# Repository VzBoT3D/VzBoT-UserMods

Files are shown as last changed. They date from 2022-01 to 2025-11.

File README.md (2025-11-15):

# VzBoT UserMods repository

Welcome to the VzBoT UserMods repository, here you may find community mods for the VzBoT 3D-printer.

<a href="https://discord.gg/Jj5C7q4j" target="_blank">Discord Shield</a>

*Remember to update this README when uploading new mod!*

There is a [contributing guide available here](./CONTRIBUTING.md).

## Directory structure

Create a folder containing your name (without spaces) and create a folder for your mod(s).

Suggested directory layout for your mod:
- creator_name/
  - mod_name/
    - README.md with a description, optionally build instructions and required parts
    - stl/ folder with stereolithographical models, oriented correctly for printing
    - cad/ folder with original design files (STEP, F3D, Scad, etc.) (optional)
    - doc/ folder with supported documentation (optional)
    - images/ folder with screen shots/renders/etc.

## Table structure

Update the following table with the information about your mod:
- Your name
- A link to your sub-folder
- A short description of your mod
- The build difficulty:
  - :green_heart: for :green_heart: (Easy)
  - :blue_heart: for :blue_heart: (Intermediate)
  - :heart: for :heart: (Advanced)

like so:
`
| Creator | [Mod title](link) | ✔️/✖️ | ✔️/✖️ | Description | Difficulty `

---

## Mods

| Creator | Mod title | Description | [Vz330](https://github.com/VzBoT3D/VzBoT-Vz330) | [Vz235](https://github.com/VzBoT3D/VzBoT-Vz235) | Difficulty
| --- | --- | --- | --- | --- | --- |
| example | [Example mod](./creator_here/mod_folder_name)| Example entry for the table | ✔️ | ✔️ | :green_heart::blue_heart::heart: |
| airox | [VZ235 Tophat](./airox/vz235_tophat)| A tophat for the vz235 | ✖️ | ✔️ | :green_heart: |
| AdderMk2 | [Patch_Cura](./AdderMk2/Patch_Cura) | Updates 2020 Tronxy profiles in Cura | ✔️ | ✔️ | :blue_heart: |
| CapnKrunchy | [Aluminum Z WAGO Mount](./CapnKrunchy/Aluminum_Z_WAGO_Mount) | WAGO mount for Aluminum Z bed assembly | ✔️ | ✖️ | :green_heart: |
| catalinutzz| [Hemera mount](./catalinutzz/hemera-mount) | Hemera mount for the VZ Printhead | ✔️ | ✔️ | :green_heart: |
| ckvsoft | [CPAP_back_panel_tube_mount_VZ330](./ckvsoft/CPAP_back_panel_tube_mount_VZ330)| CPAP back panel tube mount VZ330. | ✔️ | ✖️ | :green_heart: |
| ckvsoft | [WaveShare](./ckvsoft/waveshare_5inch_DSI_LCD)| WaveShare 5inch DSI LCD. | ✔️ | ✔️ | :green_heart: |
| der-pw | [HBVCam-3M2111_corner-mount](./der-pw/HBVCam-3M2111_corner-mount)| HBVCam-3M2111 corner-mount | ✖️ | ✔️ | :green_heart: |
| edsped | [Bowden Collet Adapter](./edsped/) | Bowden Collet Adapter  | ✔️ |  ✔️ | :green_heart: |
| EduardoMDSousa  | [Vz-Printhead Printed MGN12H](./EduardoMDSousa/Vz-Printhead-Printed-MGN12H) | VzPrinthead Printed MGN12H | ✔️ | ✔️ | :green_heart: |
| | [Vz-Printhead-Printed_Standoffs-MGN12](./EduardoMDSousa/Vz-Printhead-Printed_Standoffs-MGN12) | Vz-Printhead-Printed_Standoffs-MGN12 | ✔️ | ✔️ | :green_heart: |
| | [Vz-Printhead-Printed-MGN12H-Orbiter-1.5-Mood](./EduardoMDSousa/Vz-Printhead-Printed-MGN12H-Orbiter-1.5-Mood) | Vz-Printhead-Printed-MGN12H-Orbiter-1.5-Mood | ✔️ | ✔️ | :green_heart: |
| | [Vz-Printhead Printed Standoffs MGN12](./EduardoMDSousa/Vz-Printhead-Printed_Standoffs-MGN12) | Vz-Printhead Printed Standoffs MGN12 | ✔️ | ✔️ | :green_heart: |
|Glizzynator | [M4_Spool_Holder](./Glizzynator/M4_Spool_Holder)| Modifies the spool holder to use M4 screws instead of M3 | ✔️ | ✔️ | :green_heart: |
| jpbnto | [Y endstop](./jpbnto/yendstop) | Y-endstop using the Tronxy XS5A switch | ✔️ | ✖️ | :green_heart: |
| | [VzHextrudort heavy back plate](./jpbnto/vzhextrudort_heavy_back_plate) | Y-endstop using the Tronxy XS5A switch | ✔️ | ✖️ | :green_heart: |
| jurisv | [SLA CPAP Trihorn](./jurisv/sla_cpap_trihorn) | CPAP Trihorn Fan ducts for SLA printers as single piece | ✔️ | ✖️ | :green_heart: |
| karnadi | [NF Crazy front face](./karnadi/NF_Crazy_2510_BLTouch) | NF Crazy front face 2510 fan with BLTouch mount | ✔️ | ✔️ | :green_heart: |
| | [VzHextrudort pneumatic coupler](./karnadi/VzHextrudort_pneumatic_coupler) | VzHextrudort pneumatic PTFE coupler | ✔️ | ✔️ | :green_heart: |
| keefo | [vent hose adapter](./keefo/vent_hose_adapter) | vent hose adapter | ✔️ | ✖️ | :green_heart: |
| knarfie | [12mm Linear Rod](./knarfie/12mm_rods) | Mod for 12mm linear rods | ✔️ | ✖️ | :green_heart: |
| | [Idler Shoulder](./knarfie/shoulder_idler) | Idler mounts with spots for shoulder bolts  | ✔️ | ✖️ | :green_heart: |
| | [Trihorn](./knarfie/trihorn_duct) | Trihorn duct for the VZ Printhead | ✔️ | ✔️ | :green_heart: |
| MadduxVape | [Vz330 Duet Config](./MadduxVape) | Vz330 AWD Config for Duett board| ✔️ |  ✖️ | :green_heart: |
| marbocub | [Vz330 Y-Gantry-1515](./marbocub/Vz330_Y-Gantry-1515) | Vz330 Y-Gantry for 1515 size gantry | ✔️ |  ✖️ | :green_heart: |
| mdwasp | [Swappable Exhaust Tube](./mdwasp/swappable_exhaust_tube) | Hot-swappable exhaust tube | ? | ✔️ | :green_heart: |
| panik988 | [Sherpa + NF Crazy front face (bracket)](./panik988/sherpa_nf_crazy_bracket) | NF Crazy Face Mount with bracket for Sherpa | ✔️ | ✔️ | :green_heart: |
| pbsuper | [VZTrident](./pbsuper/VZTrident)| Tripple Z for VZbot complete printer. | ✔️ | ✔️ | :blue_heart: |
| | [Quickdraw](./pbsuper/Quickdraw)| Quickdraw for Alu Printhead. | ✔️ | ✔️ | :green_heart: |
| | [Brace_Dancer](./pbsuper/Brace_Dancer)| Brace for Dancer so Fanduct can't move sideways. | ✔️ | ✔️ | :green_heart: |
| Polar_Ted  | [VZ HextrudORT mount](./Polar_Ted/VZ_HextrudORT_High_Motor_Mount_for_EVA/) | VZ HextrudORT high motor mount for EVA print head and V6 hot end | ✔️ |  ✔️ | :green_heart: |
| | [VZ Sexbolt Z Endstop](./Polar_Ted/Sexbolt_Sidepiece_Z_Switch/) | Sexbolt side mounted Z endstop for VZ bed frame  | ✔️ |  ✔️ | :green_heart: |
| | [VZ 330 Skirt Set](./Polar_Ted/VZ330_skirt/ ) | VZ 3330 SKirt Set with V0 Display | ✔️ | ✖️ | :green_heart: |
| | [X_Y_Pully_Height_Gauge](./Polar_Ted/X_Y_Pully_Height_Gauge/) | X Y pully height gauge  | ✔️ |  ✔️ | :green_heart: |
| | [X_Y Motor Support](./Polar_Ted/X_Y_Motor_support/) | Support shelf for X and Y motors  | ✔️ |  ✔️ | :green_heart: |
| Rac | [MGN9 Gantry](./Rac/MGN9_gantry) | MGN9 gantry | ✔️ | ✔️ | ✖️ | :blue_heart: |
| rilmar | [X5SA Z](./rilmar/X5SA_Z) | X5SA Z | ✔️ | ✔️ | :green_heart: |
| RODAM 3D | [180_Hinges](./RODAM_3D/180_Hinges/) | 180 Hinges for full door open  | ✖️ |  ✔️ | :green_heart: |
| | [2WD_2_COLOR_SCREW_PACK](./RODAM_3D/2WD_2_COLOR_SCREW_PACK/) | 2 color Idler with mod for screw kit  | ✖️ |  ✔️ | :green_heart: |
| SFINAE | [Rapido HF mount](./SFINAE/Rapido_HF_30mm_fan) | Rapido HF mount for 30mm fan | ✔️ | ✔️ | :green_heart: |
| Skysi | [Beefy X-Endstop](./Skysi/Beefy%20X-Endstop) | Beefed up Enstop for X | ✔️ | ✔️ | :green_heart: |
| SSerpente  | [Klicky probe](./SSerpente/Klicky%20probe%20Vzbot) | Klicky probe mount | ✔️ | ✔️ | :green_heart: |
| treintjes  | [Skirt](./treintjes/VzBot_Skirt) | Skirt for the VZ-Bot to house electronics under the frame | ✔️ |  ✖️ | :green_heart: |
| MadduxVape | [Vz330_Duet_Config](./MadduxVape) | Vz330 AWD Config for Duett board| ✔️ |  ✖️ | :green_heart: |
| zxzimeng  | [12mm rod aligner](./zxzimeng/12mm_aligner/) | 12mm Z Rod Aligner  | ✖️ |  ✔️ | :green_heart: |
| Lobod | [VzHextrudORT Optical Filament Sensor](./Lobod/VzHextrudORT_Filament-Sensor/) | Optical Filament sensor for printed VzHextrudORT | ✔️ | ✔️ | :heart: |

<sub>Credits to [VoronDesign/VoronUsers](https://github.com/VoronDesign/VoronUsers)</sub>

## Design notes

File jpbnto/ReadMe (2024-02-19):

YendStop.stl - using the stock tronxy x5sa limit switch, mounting position front left or rear right
Added vz hextrudort heavy backplate (note: gear spacing is for BMG clone gears)
Added klicky-00 fan duct.stl

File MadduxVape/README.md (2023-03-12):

Vz330 built from a folgertech ft5 frame 
duet wifi with a duex board this firmware is designed with cpap fan setup can easily be modified to your needs.
go through basic setup recieve updates replace files with the once included in zip folder and make the minor changes for your machine
has bl touch installed

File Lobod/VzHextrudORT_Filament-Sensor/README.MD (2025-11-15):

# Better filament sensor for VzHextrudORT

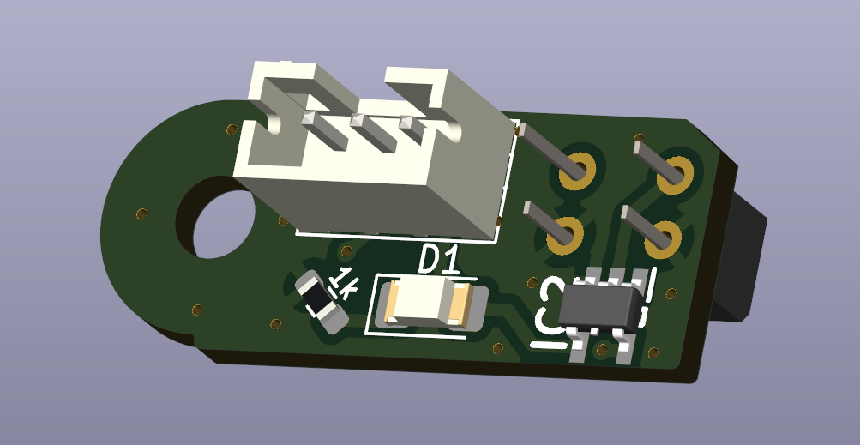
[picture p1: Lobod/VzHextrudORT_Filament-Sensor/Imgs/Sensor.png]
Sensor


Based on ERCF Binky and has the same BOM.
Uses similar principle as hall effect filament sensor, but utilizes optical path blocking for triggering.

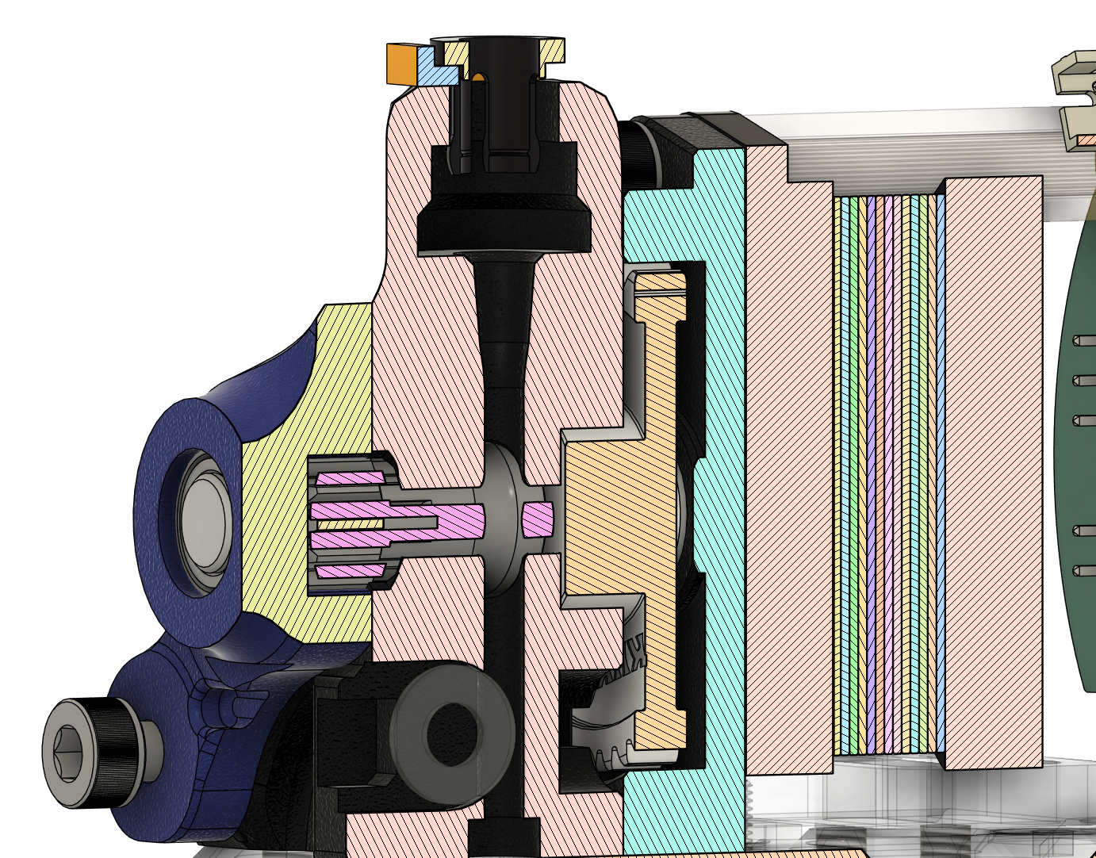
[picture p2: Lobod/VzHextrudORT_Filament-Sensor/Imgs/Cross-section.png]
Cross-section

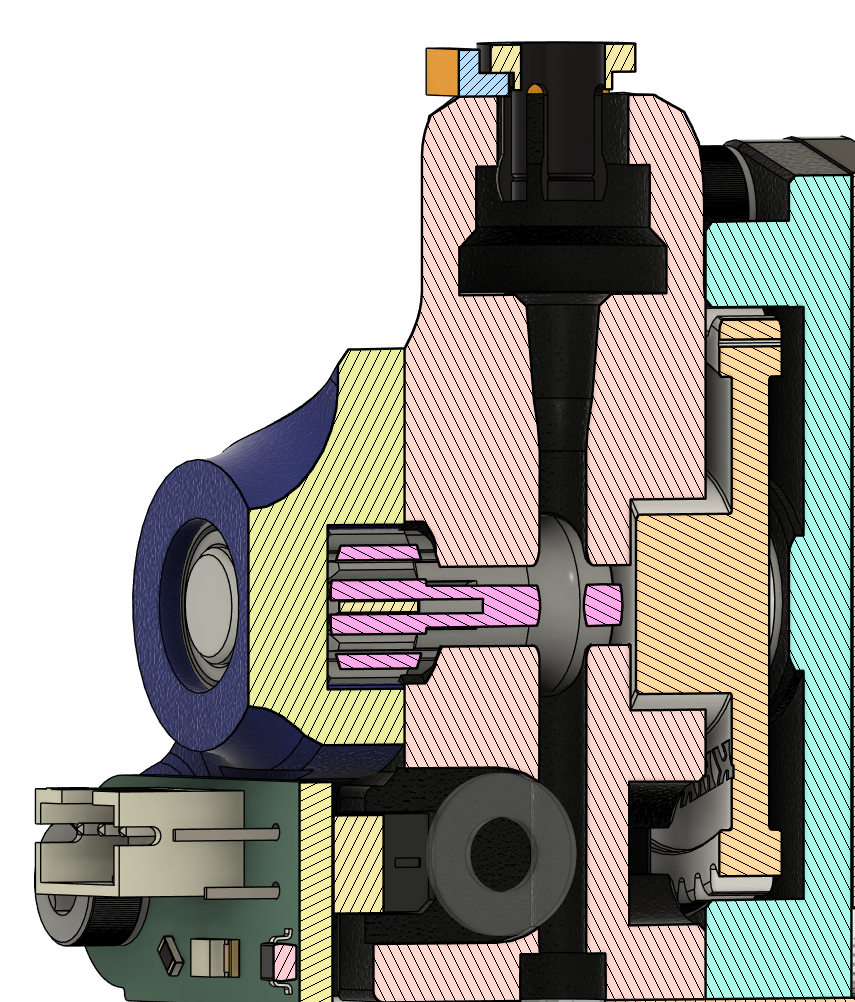
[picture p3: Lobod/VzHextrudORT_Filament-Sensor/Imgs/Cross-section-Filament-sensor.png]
Cross-section


# BOM
The same as in the original Extruder **except 6x3mm magnet**

# PCB BOM
| Component | Symbol  | Footprint |
|---|:---|:---|
Capacitor 0.1µF|C2|0603
Resistor 10K|R1|0603
Resistor 1K|R2|0603
Resistor 330R|R3|0603
LED Diode|D1|1206
EE-SX1103|IC1|EESX1103
SN74LVC1G14DBVR|IC1|SOT95P280X145-5N
JST PH 3pin|J1|JST_PH_B3B-PH-K_1x03_P2.00mm_Vertical

Interactive BOM can be found in ./PCB/BOM/ibom.html

# Build
1. Order PCB from a manufacturer.
    Ones I have tested in the past: OSHPark, JLCPCB, PcbWay.

2. Solder all parts to their coresponding places (for now there is no possibility to get soldered sensors).

3. Print included STLs (You may use supports in magnet section).

4. Place 6x3mm Magnet in the printed slot.

5. Press fit sensor into the printed base.

6. Enjoy!

# PCB Images
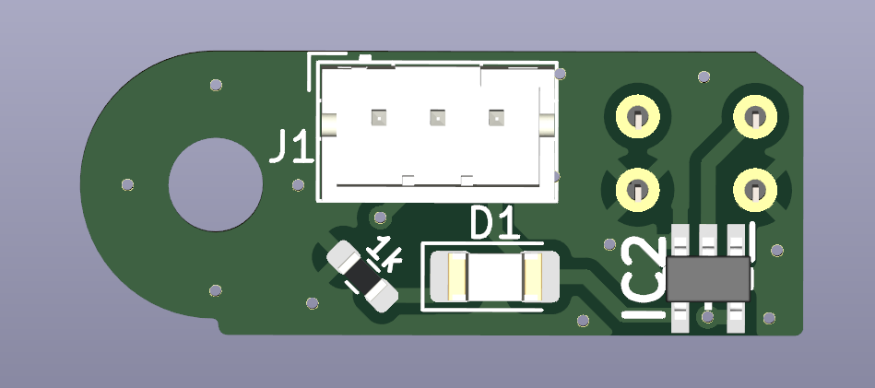
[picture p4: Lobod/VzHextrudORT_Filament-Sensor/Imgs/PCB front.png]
PCB-Front

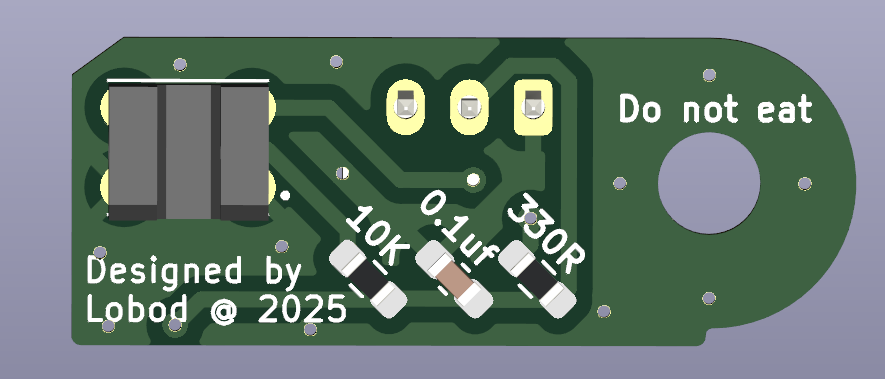
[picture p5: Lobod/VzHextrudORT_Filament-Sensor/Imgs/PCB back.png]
PCB-Back


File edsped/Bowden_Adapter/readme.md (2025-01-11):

Bowden Clip Adapter Using Spec'ed Mellow Collets, LARGE, and E3D Collets, SMALL.

I can't remember what length of screw was originally provided with the extruder but will need at least a 20mm long screw.

Print with top of adapter face down on print surface as oriented in the stl file, supports not needed.

Files on printables...

https://www.printables.com/model/486241-bowden-clip-adapter-for-vz-hextrudort-cnc-using-th

https://www.printables.com/model/420994-bowden-clip-adapter-for-vz-hextrudort-cnc-using-th

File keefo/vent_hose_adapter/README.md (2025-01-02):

this adapter can install on the outside of the vzbot exhaust filter, to connect a 3inch vent hose.

BOM:

1. M3x30mm screws x 4. (vzbot offical doc use 25mm M3 here)
2. A 3 inch flexible vent hose, length based on your needs. Like this one on amazon: https://a.co/d/2pFttcT

Print with:
* 0.2mm layer height. 
* with support, 
* 15%~30% infill.
* Nice to print it in ABS, PLA also works.

If you use this hose, you can remove the hepa filter to increase the air flow. You can save some money on buying hepa filter.  

I kept the activated carbon vent filter in to prevent bugs coming.

Showcase:

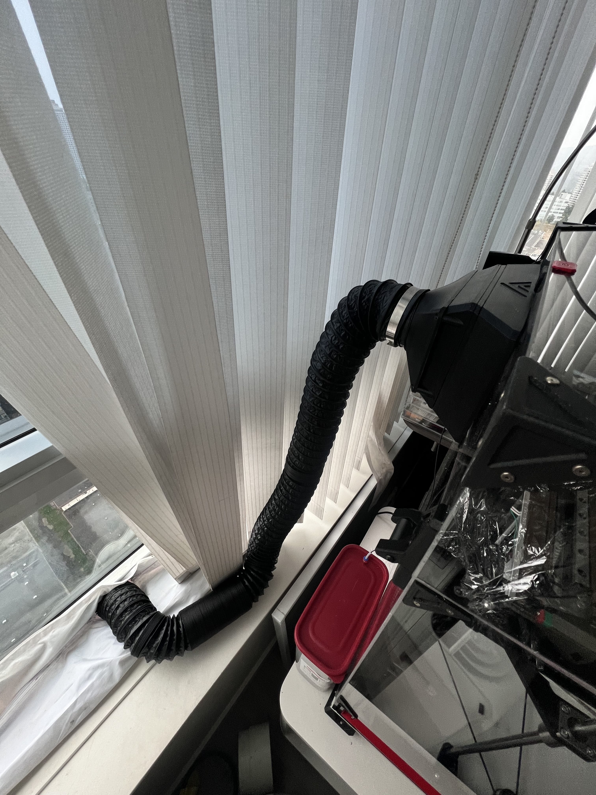
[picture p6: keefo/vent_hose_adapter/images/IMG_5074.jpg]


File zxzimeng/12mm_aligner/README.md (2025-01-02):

12mm Rod Aligner for [knarfie's 12mm rod mod](https://github.com/VzBoT3D/VzBoT-UserMods/tree/master/knarfie/12mm_rods)  
Drop in for the [10mm Aligner](https://github.com/VzBoT3D/VzBoT-Vz235/blob/main/Assemblies%20%26%20STL/Tools/Z%20allignment%20tool%2010mm%20rod%20VZ235%20VZ%20printhead.stl), using the same center position.

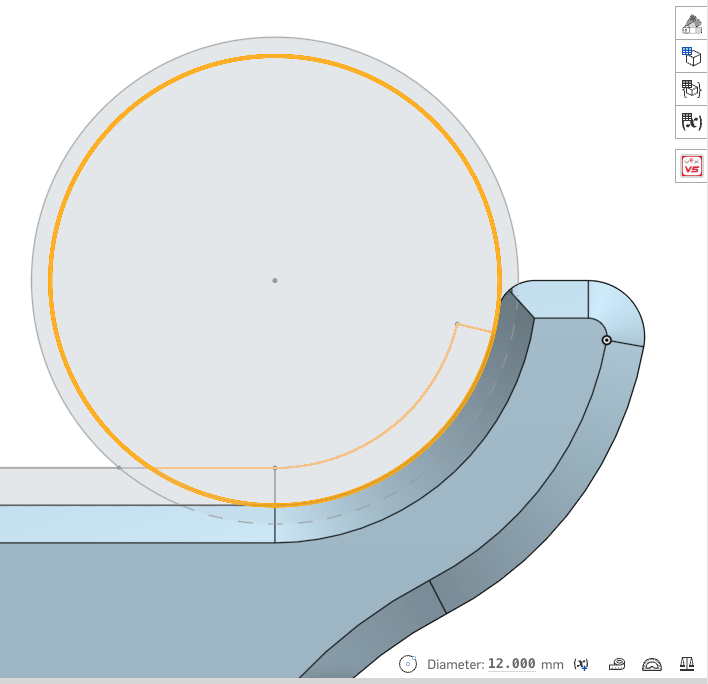
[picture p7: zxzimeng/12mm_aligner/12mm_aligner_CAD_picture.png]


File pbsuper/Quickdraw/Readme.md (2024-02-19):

Quickdraw mount for VZbot Alu Printhead.

Quickdraw 1 is the original older version. We have since updated to Quickdraw 2 and i would recommend everyone to use that.

Strip 2 24AWG wires for about 2cm twist the wire so no strands are loose and stick it in the back of the Quickdraw mount. Cut wires flush with magnets after they have been added into the mount and put a dot of glue on the wire where it enters the Quickdraw Mount. For added security you can add a tiny dot of solder onto the wire/magnet where they touch. be carefull not to heat the magnet since it will loose it's strength then.

The printed Printhead version is made for the backplate without tensioners. If you still tension your belts at the backplate this won't fit.

QD1 BOM
```
6x3mm Magnets 6x
M3 Heat inserts 8x
15cm 24AWG wire 2x
M2x10mm socket head NOT RVS/Stainless. Needs to be attracted to magnets.
Omron D2F-5 1x
```

QD2 BOM
```
6x6mm Magnets 4x
M3 heat inserts 4x
M3 Nut 1x
15cm 24AWG wire 2x
Omron D2F-5 1x
6x3-3mm ring magnets 2x [ring magnet](https://www.aliexpress.com/item/1005003026319118.html?)
M3x8mm Ultra Flat Head bolt Black 2x [Ultra Flats](https://a.aliexpress.com/_uH3ne5)
M3x12mm Button head or Ultra flat head 1x
M2x10mm Self tapping Button head NOT RVS/Stainless. Needs to be attracted to magnets.
```

To use quickdraw a module needs to be added.

SSH into your Pi with a application like Putty and type:
```
cd ~/klipper/klippy/extras
wget https://raw.githubusercontent.com/cloakedcode/klipper/work-annex-probe/klippy/extras/dockable_probe.py
sudo service klipper restart 
```
For more info go to [Quickdraw](https://github.com/Annex-Engineering/Quickdraw_Probe)
Credits to Annex-Engineering for designing it.

Example Config for VZTrident 400 on BTT Octopus board WIth QD1:
```
[dockable_probe]
pin: PG10
x_offset:                          26 # offset for microswitch x direction off nozzle
y_offset:                          56 # offset for microswitch y direction off nozzle
z_offset:                          6.42 # offset for microswitch in z height

samples:                           3
sample_retract_dist:               3 # this is so the machine has time for the switch to reset properly, especially with a higher retract speed
samples_result:                    median
samples_tolerance:                 0.04
samples_tolerance_retries:         3
speed:                             15 # do not go higher than 10mm/s, you will destroy the switch
lift_speed:                        20
z_hop:                             15.0

attach_speed:                      8
detach_speed:                      10
travel_speed:                      300

approach_position:		   380,380, 25 #you need to set these on your own
detach_position:		   360,330 #you need to set these on your own
dock_position:            	   390,380, 25 #you need to set these on your own
dock_retries:			   3

check_open_attach:                 True #checks to see if the probe is attached before moving the toolhead, if not retries to pick up the probe
auto_attach_detach: True
```

Example Config for the VZ235 with BTT Octopus Board with QD2:
``` 
[dockable_probe]
pin: PG10
x_offset:                          26 # offset for microswitch x direction off nozzle
y_offset:                          56 # offset for microswitch y direction off nozzle
z_offset:                          6.42 # offset for microswitch in z height

samples:                           3
sample_retract_dist:               3 # this is so the machine has time for the switch to reset properly, especially with a higher retract speed
samples_result:                    median
samples_tolerance:                 0.04
samples_tolerance_retries:         3
speed:                             15 # do not go higher than 10mm/s, you will destroy the switch
lift_speed:                        20
z_hop:                             15.0

attach_speed:                      8
detach_speed:                      10
travel_speed:                      300

approach_position:		   162,220,20 #you need to set these on your own
detach_position:		   100,240,20 #you need to set these on your own
dock_position:            	   162,240,20 #you need to set these on your own
dock_retries:			   3

check_open_attach:                 True #checks to see if the probe is attached before moving the toolhead, if not retries to pick up the probe
auto_attach_detach: True
```

You also need to use a Safe_Z_Home to let it know where to move to to home Z.

```
[safe_z_home]
home_xy_position: 200,200 # set this to the center of your bed.
speed: 200
z_hop:20
z_hop_speed: 30
```

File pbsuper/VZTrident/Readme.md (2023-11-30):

# VZTrident
VZTrident the VZbot Trident child.

These builds are all VZbot sizes with triple Z sytem if you prefer Trident Z or Ratrig Style we have it both:

VZbot Gantry and tophat hinges.

Trident Skirt

Annex engineering Panel clips and Door Hinges for the 400 and 330 size.

Triple Z system inspired by the Trident and Ratrig.

Video of the 400 size printer: [VZTrident](https://drive.google.com/file/d/1hXe_eZGZ0fsk1MWA-nmpsxVc_xzYL8Yt/view?usp=sharing)



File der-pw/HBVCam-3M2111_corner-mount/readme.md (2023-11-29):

## Corner bracket mounting for a HVBCam 

The camera can be mounted in the top left corner. It is possible to lead the cable out backwards in one of the profiles. If you use the HBVCam-3M2111, you have a view angle of 110° and thus a complete overview of the print bed. With this arm, it fits nicely at the Vz235, It is quite possible that it also fits on the Vz330, but untested.

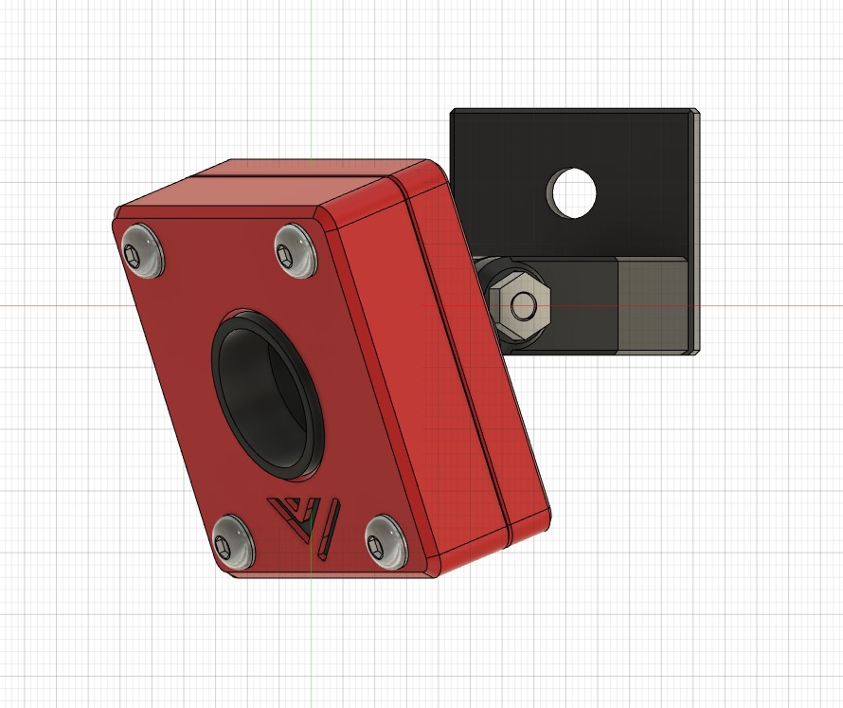
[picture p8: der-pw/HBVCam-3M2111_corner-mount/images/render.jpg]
render of the camera

---

You need:

| amount |  | Description
| --- | --- | ---
| 5x | 12mm x M2.5 | button head screws
| 2x | 6mm x M2.5 | button head screws
| 7x | M2.5 | nuts
| 1x | M4 | 10mm screw
| 1x | xxx | slot nut

---

The camera has not the best quality, see for yourself, but it is sufficient for monitoring the printing room.

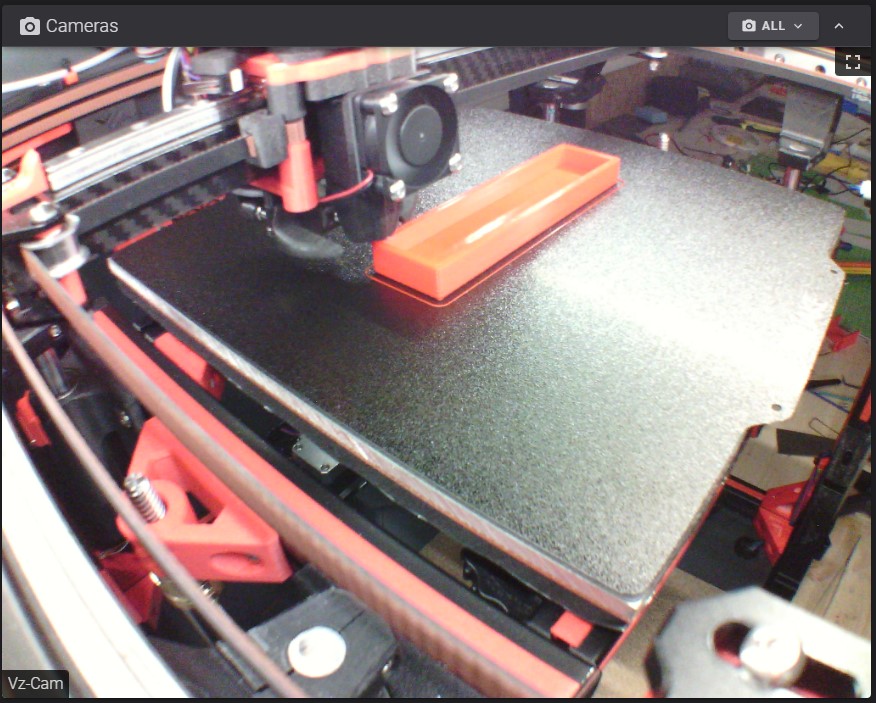
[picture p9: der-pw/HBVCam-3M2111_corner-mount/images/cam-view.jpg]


---

First screw "Bracket_Part1" to the rear half of the case. Use the M2.5x6 screws for this.
Then the lens has to be unscrewed. But this is possible without any problems. Then you put the camera in the front housing shell, after that put the lens back on to protect the sensor from dust and specks. Put the rear case shell on and screw both halves tight. Use the M2.5x12 screws. Screw the "Bracket_Part2" to the "Bracket_Part1" using the M2.5x12 screw.
The case should be finished. Now you can attach the camera into the top left corner of your Vz235.

---

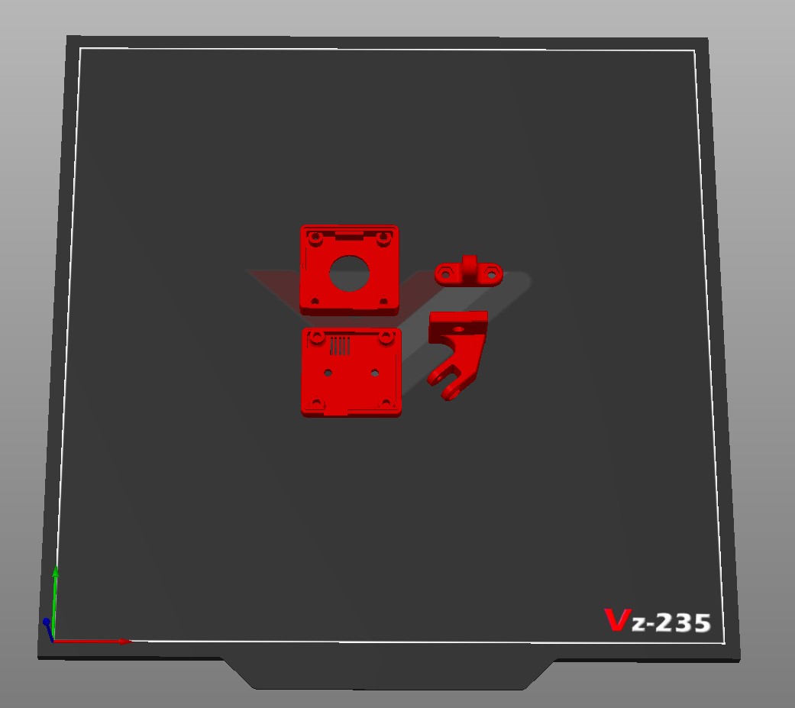
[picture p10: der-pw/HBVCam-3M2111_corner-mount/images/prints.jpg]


---

This contribution was made by [der-pw](https://github.com/der-pw).  
STEP-File inside, feel free to edit, improve or modify this thing, but respect the [CC BY-SA 4.0](https://creativecommons.org/licenses/by-sa/4.0/) license.

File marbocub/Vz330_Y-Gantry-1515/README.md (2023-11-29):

# Vz330 Y-Gantry-1515

This is the Y gantry bottom parts for the VzBoT Vz330. They are used to replace X gantry to lower cost, lighter weight 1515 size instead of 2020 size.

### examples of 1515 size rods
|Type|Weight(440mm)|Moment of inertia of area|
|---|---|---|
|A6063S−T5 square tube 15x15xt1.5|97g|0.249×10<sup>4</sup> mm<sup>4</sup>|
|Misumi HFS3-1515|150g|0.280×10<sup>4</sup> mm<sup>4</sup>|
|MakerBeamXL|147g||

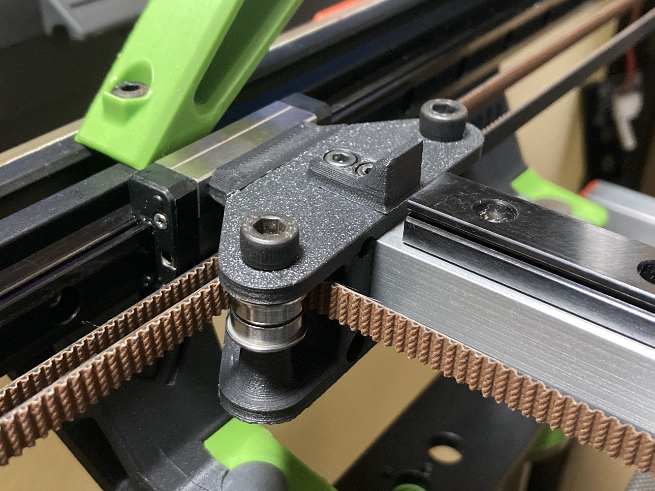
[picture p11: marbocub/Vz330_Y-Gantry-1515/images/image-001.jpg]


The geometry and shape is based on the Vz330 V1.2's Y gantry except for minor differences and is fully compatible.

note: After the Vz330 V1.2 is released, the left and the right of the Y gantry are not common parts.  If you are using less than V1.2, please re-printing and combining Y-gantry-top-left and Y-gantry-top-right released by official VzBoT.

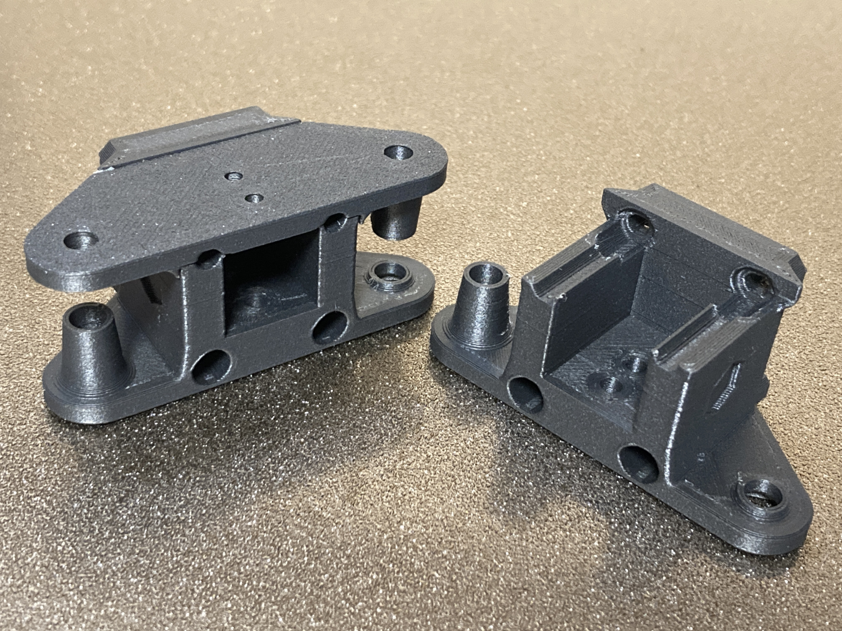
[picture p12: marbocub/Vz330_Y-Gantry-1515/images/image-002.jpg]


Side dimple marks show the direction of the part. Illustrated below are the left part, the tooth side is the front and the smooth side is the back.

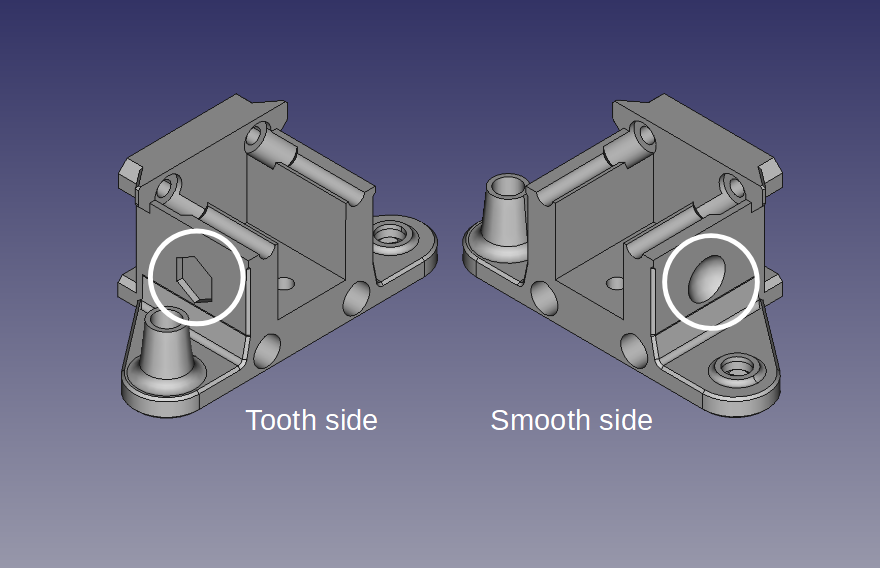
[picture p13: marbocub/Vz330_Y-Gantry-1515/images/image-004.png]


## BOM

|Part|STL|PCs|
|---|---|---|
|Left Bottom|This Y_gantry_1515_bottom_left-15.0.stl|1|
|Right Bottom|This Y_gantry_1515_bottom_right-15.0.stl|1|
|Left Top|The official Vz330 V1.2's Y_gantry_top_left.stl|1|
|Right Top|The official Vz330 V1.2's Y_gantry_top_right.stl|1|
|X end stop|The official Vz330 V1.2's XendStop.stl|1|

If the fitting is tight you can use *_15.1-looser.stl instead of *_15.0.stl for fit looser.

## Tested

### Using a 1515 gantry:

I have long term tested using an aluminium 15x15xt1.5 square tube and a MGN12H for X gantry about one year and confirmed there are not really any problems for printing.

### This Y-Gantry-1515:

They are printed IEMAI CF-ABS and tested over the 3 months of 300-600mm/s high speed printings and do not show any problems.

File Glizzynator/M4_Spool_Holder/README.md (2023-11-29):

# M4 Spool Holder
This is a simple mod that allows the use of M4 screws to attach the spool holder to the frame and moves the PTFE insertion hole at the back so it cannot escape and does not have a hole on the side. A version with a front facing hole is also available.

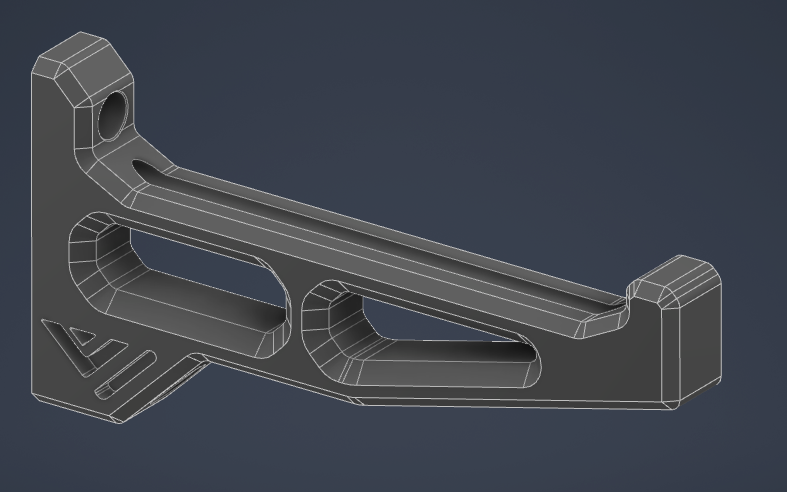
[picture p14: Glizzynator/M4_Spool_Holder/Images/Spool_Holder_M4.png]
M4_Spool_Holder


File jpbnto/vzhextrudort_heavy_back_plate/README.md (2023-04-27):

# vzhextrudort heavy back plate

[vzhextrudort heavy back plate.stl](./vzhextrudort%20heavy%20back%20plate.stl)

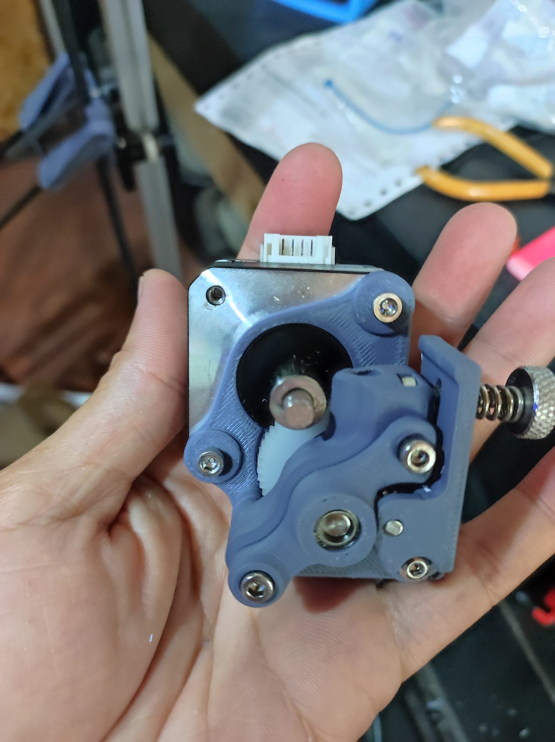
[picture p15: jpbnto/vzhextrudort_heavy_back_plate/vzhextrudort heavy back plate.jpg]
vzhextrudort heavy back plate.jpg


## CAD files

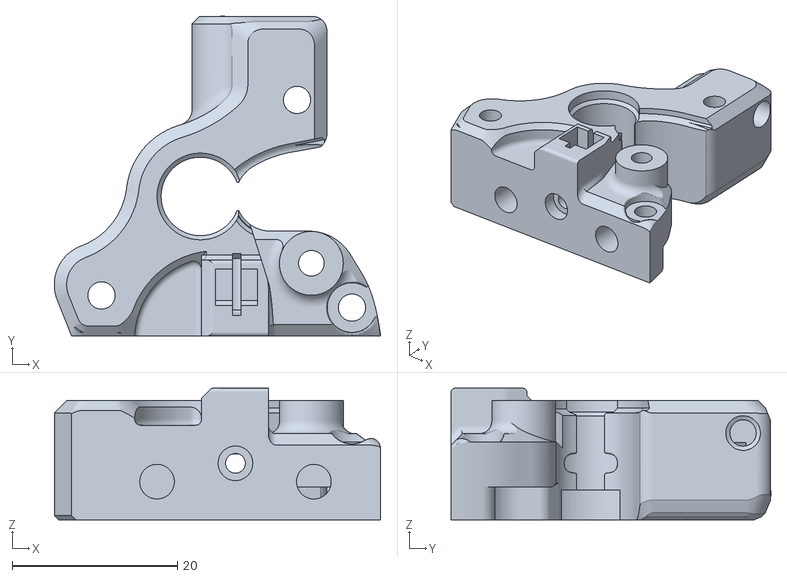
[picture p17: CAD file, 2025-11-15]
Lobod/VzHextrudORT_Filament-Sensor/STL/FilamentSensor_Main-Body-RIDGA-ERCF.stl
39.5 x 38.8 x 16.0

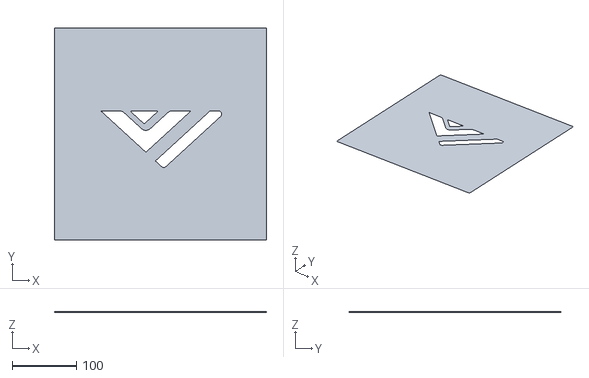
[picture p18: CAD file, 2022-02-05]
AdderMk2/Patch_Cura/resources/meshes/VzBot.stl
330.0 x 330.0 x 1.00

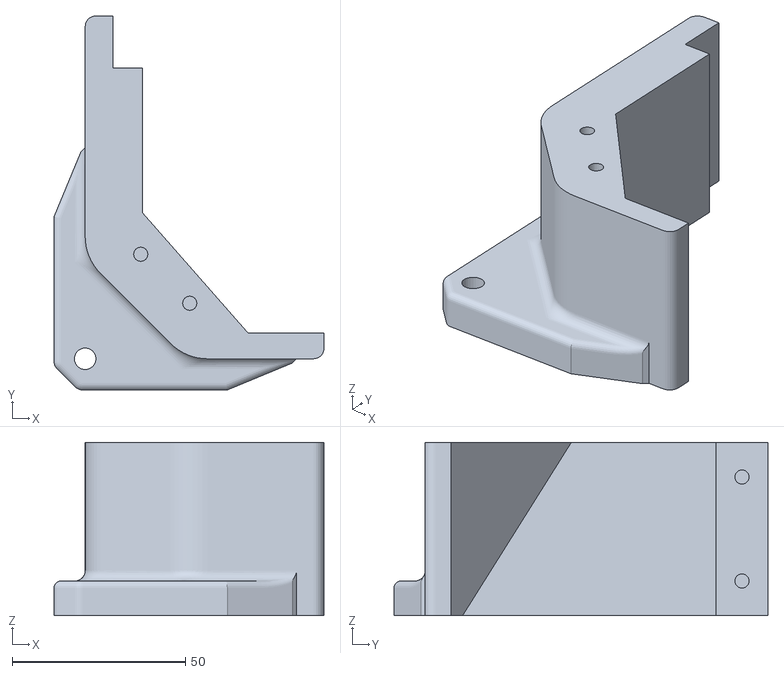
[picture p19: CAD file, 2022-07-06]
airox/vz235_tophat/stls/Corner_FrontLeft.stl
77.9 x 107.9 x 50.0

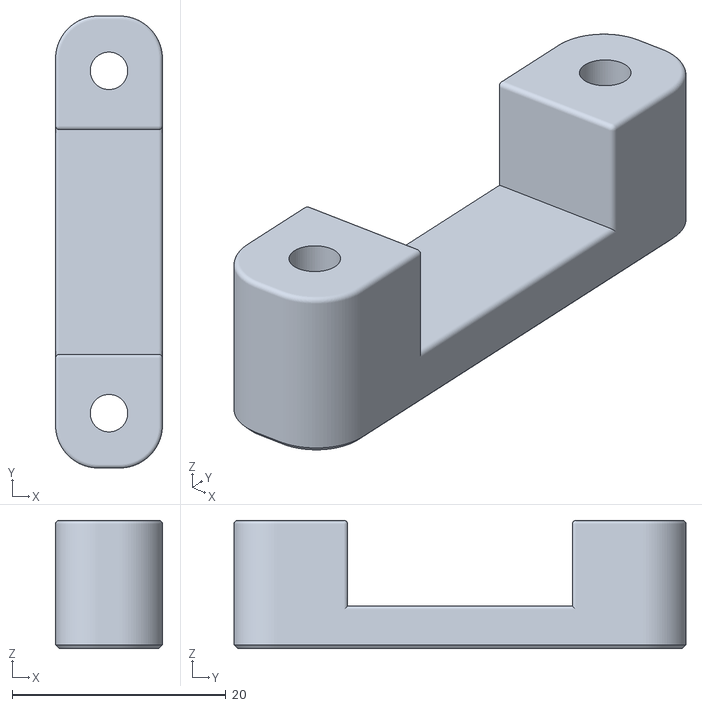
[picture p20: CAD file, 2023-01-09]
CapnKrunchy/Aluminum_Z_WAGO_Mount/STLs/AluZ_Wago_Clamp_x2.stl
10.0 x 42.3 x 12.0

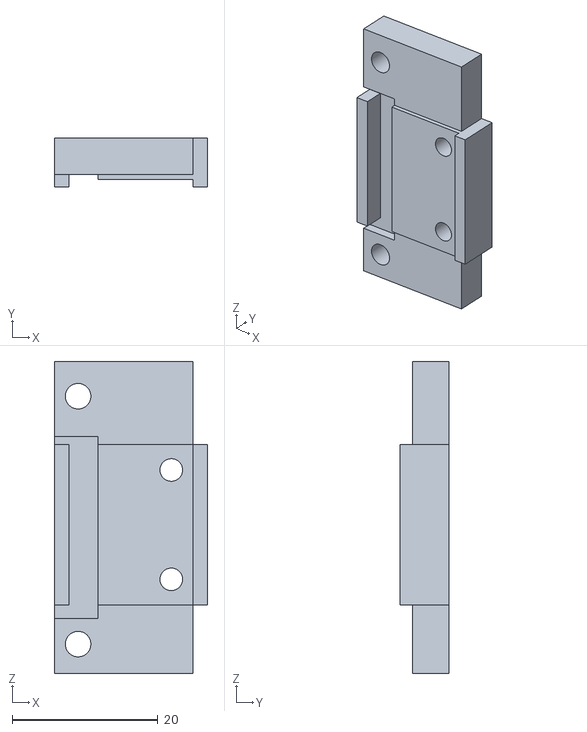
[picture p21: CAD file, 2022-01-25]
catalinutzz/hemera-mount/stl/removable adxl345.stl
21.1 x 6.70 x 42.8

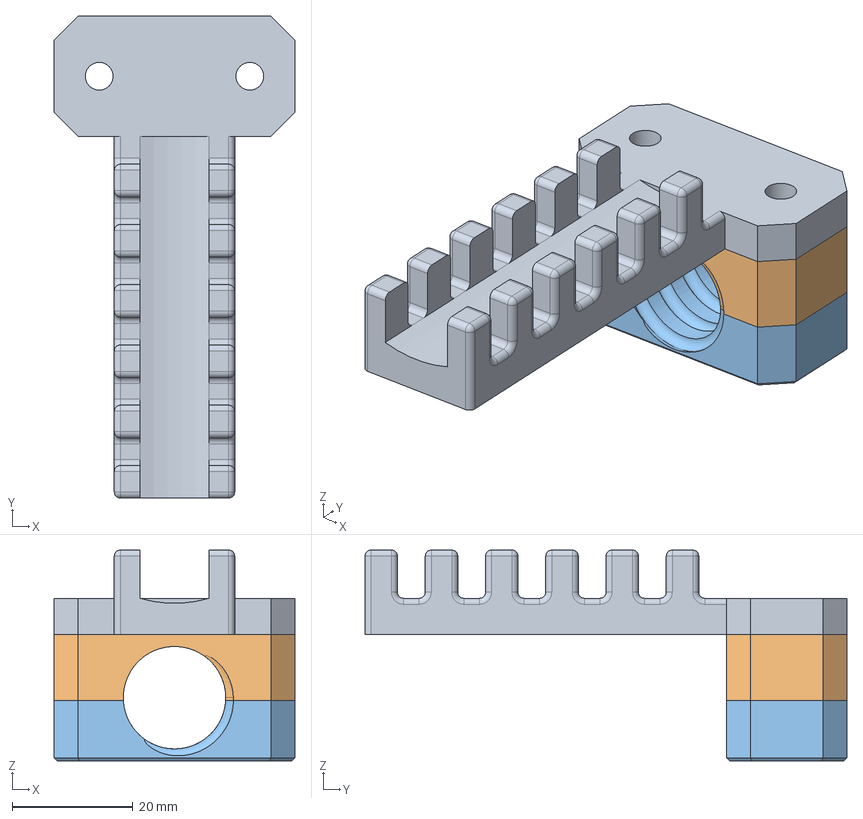
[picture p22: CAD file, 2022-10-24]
ckvsoft/CPAP_back_panel_tube_mount_VZ330/step/CPAP_back_panel_tube_mount_VZ330.step
40.0 x 80.0 x 35.0 mm

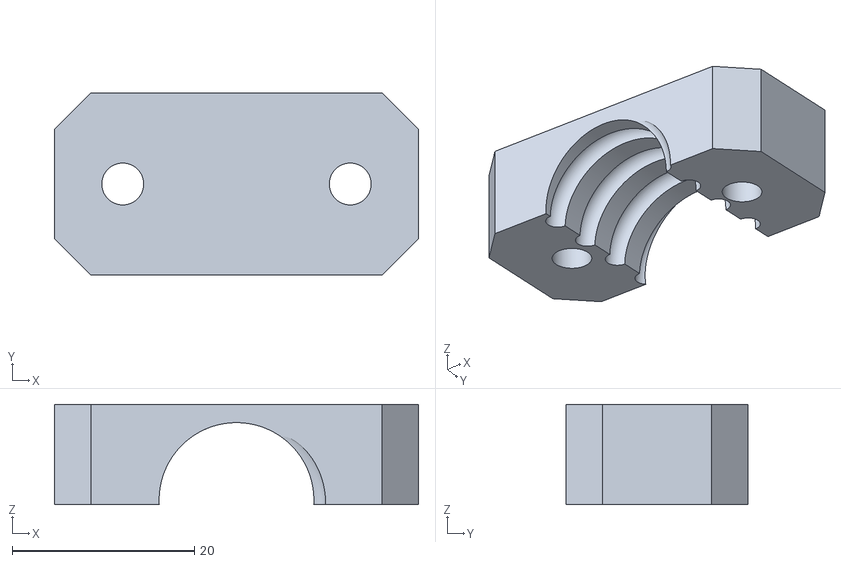
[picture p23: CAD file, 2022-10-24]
ckvsoft/CPAP_back_panel_tube_mount_VZ330/stl/CPAP_back_panel_tube_mount_VZ330_part2.stl
40.0 x 20.0 x 11.0

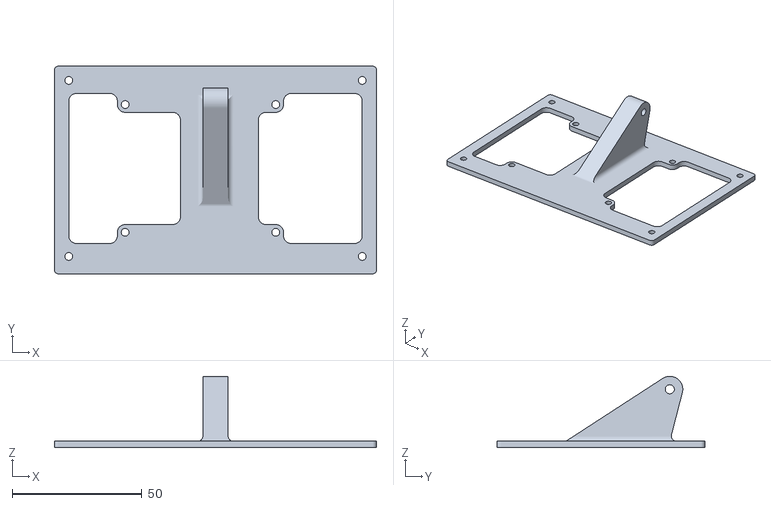
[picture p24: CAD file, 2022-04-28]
ckvsoft/waveshare_5inch_DSI_LCD/stl/screen mount back.stl
124.0 x 80.0 x 27.5

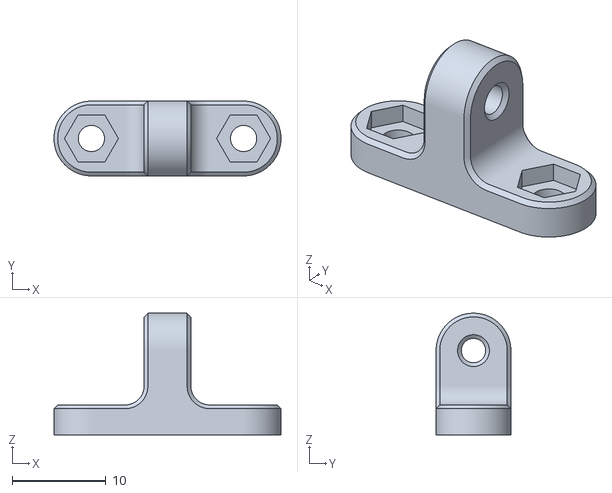
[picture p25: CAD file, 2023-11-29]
der-pw/HBVCam-3M2111_corner-mount/stl/Bracket_Part1.stl
24.3 x 8.00 x 13.0

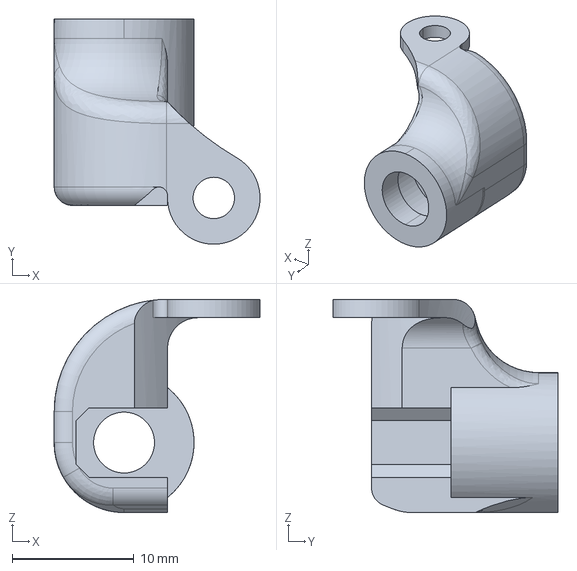
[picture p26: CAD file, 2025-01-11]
edsped/Bowden_Adapter/cad/bowden_clip-big.stp
16.9 x 18.5 x 17.5 mm

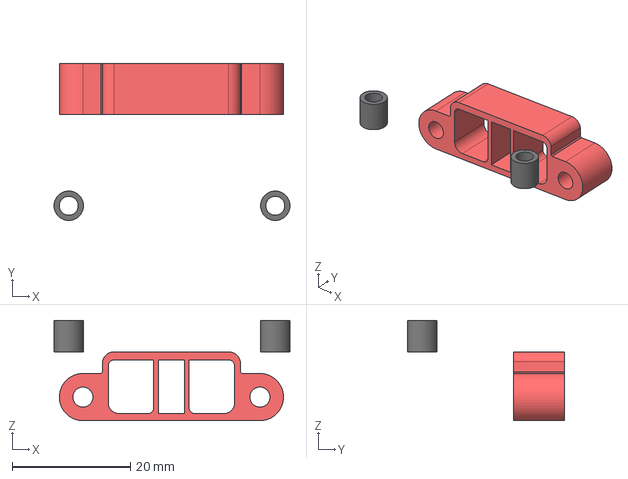
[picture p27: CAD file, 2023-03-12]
EduardoMDSousa/Vz-Printhead-Printed-MGN12H-Orbiter-1.5-Mood/CAD/Extra Printed parts fo MGN12H Vz-Printhead/Cariage mgn12 Extra parts V2.step
40.0 x 26.6 x 17.0 mm
trihorn spacer For Rapido MGN12H V2
duct spacer trihorn MGN12H

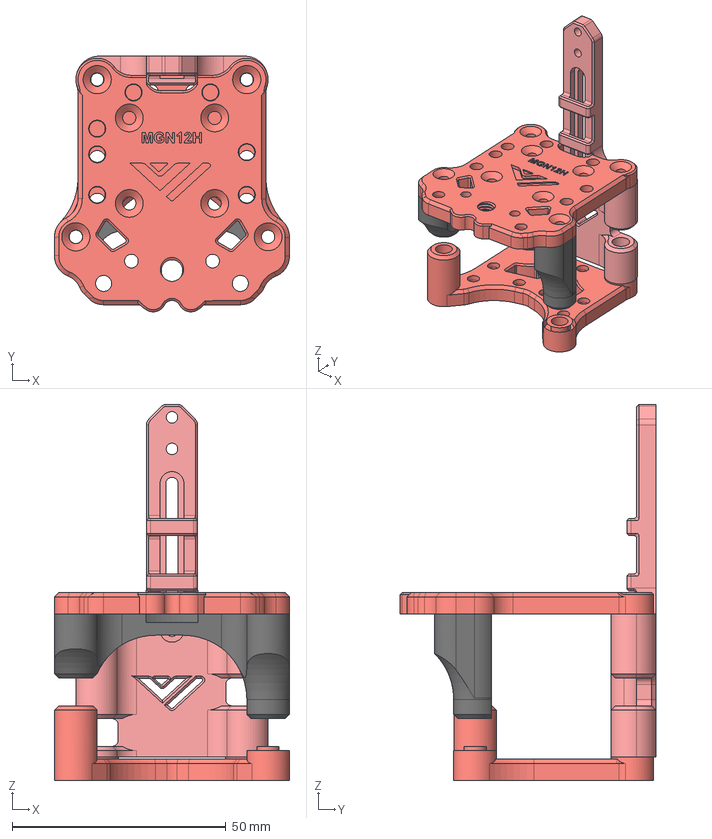
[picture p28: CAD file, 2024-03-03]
EduardoMDSousa/Vz-Printhead-Printed-MGN12H-Orbiter-1.5-Mood/CAD/Vz-Printhead Printed MGN12H cariage+Hardwear/carriage mgn12 v2 Beta 8 v1.0.step
55.0 x 59.9 x 88.0 mm
back plate MGN12H v2
Front MGN12H v2
Top plate MGN12H
bottom plate NGN12H V1

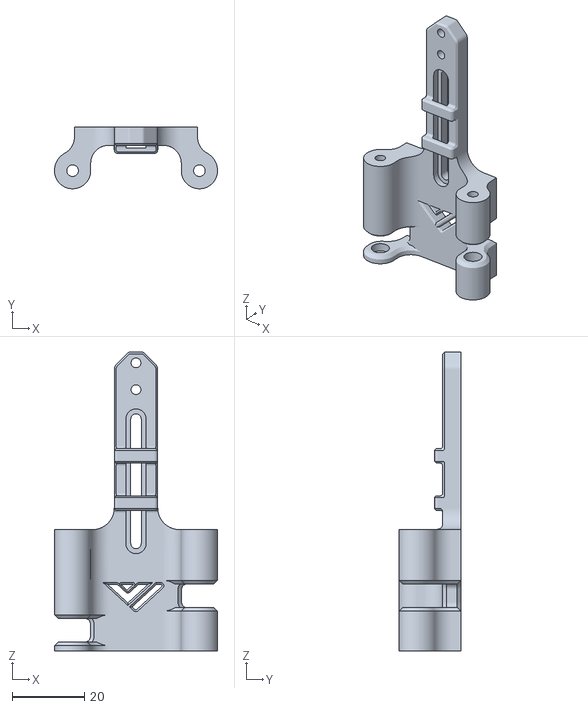
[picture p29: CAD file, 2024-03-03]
EduardoMDSousa/Vz-Printhead-Printed-MGN12H-Orbiter-1.5-Mood/STLs/carriage/back plate MGN12H v2 (orbiter1.5).stl
45.0 x 17.0 x 82.5

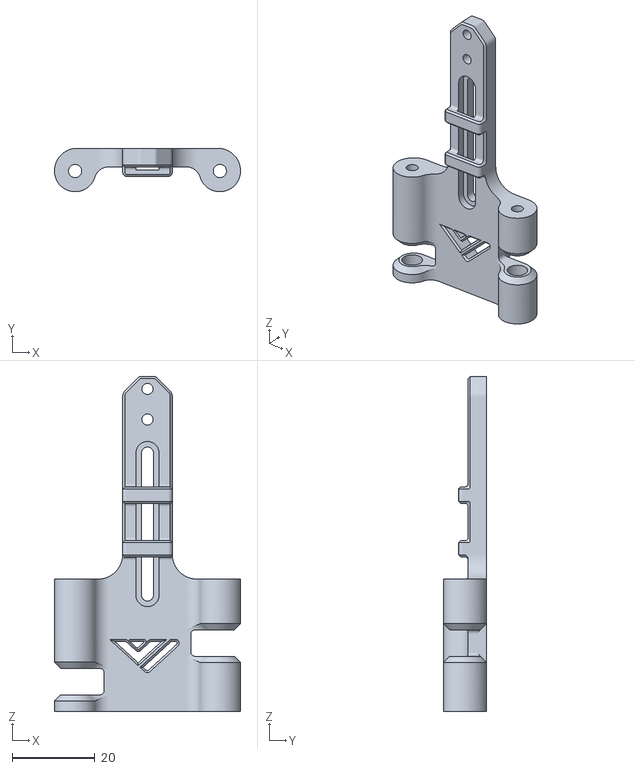
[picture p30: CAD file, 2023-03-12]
EduardoMDSousa/Vz-Printhead-Printed-MGN12H/STLs/carriage/Back plate.stl
45.0 x 10.5 x 81.0

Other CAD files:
EduardoMDSousa/Vz-Printhead-Printed-MGN12H/STLs/part cooling ducts wprobe dock/Regular Klicky/Klicky_Trihorn Fan Duct v3.3mf
EduardoMDSousa/Vz-Printhead-Printed-MGN12H/STLs/part cooling ducts+MGN12 Extra/CPAP duct MGN12H.3mf
EduardoMDSousa/Vz-Printhead-Printed_Standoffs-MGN12/STLs/bottom plate V4.3 MGN12 (Plastic Standoffs) (tubes).stl
Glizzynator/M4_Spool_Holder/STEP/Spool_Holder_M4_Front_Hole.stp
CapnKrunchy/Aluminum_Z_WAGO_Mount/CAD/VZ330-AluZ-BedWago.f3d
CapnKrunchy/Aluminum_Z_WAGO_Mount/STLs/AluZ_Wago_Mount.stl
EduardoMDSousa/Vz-Printhead-Printed-MGN12H-Orbiter-1.5-Mood/CAD/Vz-Printhead Printed MGN12H cariage+Hardwear/carriage mgn12 v2 Beta 8.step
EduardoMDSousa/Vz-Printhead-Printed-MGN12H-Orbiter-1.5-Mood/STLs/carriage/Belt_clip.stl
EduardoMDSousa/Vz-Printhead-Printed-MGN12H-Orbiter-1.5-Mood/STLs/carriage/Front MGN12H v2.3mf
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

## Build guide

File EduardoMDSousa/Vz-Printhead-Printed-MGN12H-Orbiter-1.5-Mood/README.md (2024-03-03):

# Vz-Printhead-Printed-MGN12H-Orbiter-1.5-Mood
Vz-Printhead-Printed-MGN12H-Orbiter-1.5-Mood

BETA ! TESTED ! We need help from the community to test and report feedback. Use at your own risk
The Vz-Printhead Printed MGN12H Version

The Vz-Printhead is a light weight and stiff head made for the VzBoTs, with MGN12H on X Axis. It was designed to be compatible with almost all hotends, and extruders out there, "and now with Orbiter 1.5 to". With the height adjustable fan duct, you can easily change your config without having to re-print a new fan duct.

Note, it may be necessary to print extra parts depending on the hotend to use, the extra parts in the STL folders are for Goliath and Rapido, also the new CPAP duct to print as well, as the extruder adapter plate.
_ _ _ _ _ _ _ _ _ _ _ _ _ _ _ _ _ _ _ _ _ _ _ _ _ _ _ _ _ _ _ _ 
Atencion.
Note, Since the top plate is the same, it is only needed to print the adapter plate and the back plate to fit this mood, all other partes are the same.
_ _ _ _ _ _ _ _ _ _ _ _ _ _ _ _ _ _ _ _ _ _ _ _ _ _ _ _ _ _ _ _ 

Spacers and so on, can be edited in cad and exported for printing, if any user can't edit I'll be happy to help edit and export the essentials.

in the extra parts folder, the head doc for Klicky prob and NRG versions will also be available

Hope you like and be useful for any one.

you can find me on the Facebook Group as Eduardo Sousa or on discord @EduardoSousa#7556

ps. My thanks to Simon Vez , for his great help with advice and revision.

Credits, from the original version and Readme, go to Simon Vez






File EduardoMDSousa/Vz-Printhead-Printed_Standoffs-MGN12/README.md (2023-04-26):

# Vz-Printhead-Printed Printed-Standoffs-MGN12 Mood
Vz-Printhead-Printed Printed-Standoffs-MGN12 Mood

 We need help from the community to test and report feedback. Use at your own risk
The z-Printhead-Printed Printed-Standoffs-MGN12 Version

The Vz-Printhead is a light weight and stiff head made for the VzBoTs, with MGN12H an C on X Axis. It was designed to be compatible with almost all hotends, and extruders out there. With the height adjustable fan duct, you can easily change your config without having to re-print a new fan duct.

In this Mood, the top plate MGN12 H or C is the same as the official version in the main repository, all the duct etc are the same, for that reason those parts are not available here.

here are just the essential parts for the mood.

Note this mood uses 4 M3x45mm screws and 4 M3 lock nuts

It is available Good with description of the parts to facilitate the assembly.

Note, it may be necessary to print extra parts depending on the hotend to use, the extra parts in the STL folders are for Goliath and Rapido, also the new CPAP duct to print as well.

Spacers and so on, can be edited in cad and exported for printing, if any user can't edit I'll be happy to help edit and export the essentials.

in the extra parts folder, the head doc for Klicky prob and NRG versions will also be available

you can find me on the Facebook Group as Eduardo Sousa or on discord @EduardoSousa#7556

ps. My thanks to Simon Vez , for his great help with advice and revision.

Credits, from the original version and Readme, go to Simon Vez

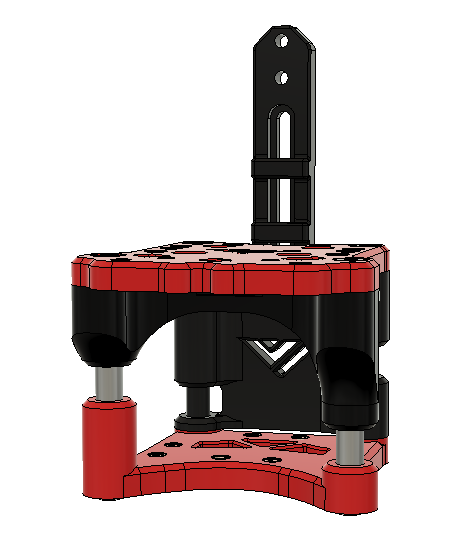
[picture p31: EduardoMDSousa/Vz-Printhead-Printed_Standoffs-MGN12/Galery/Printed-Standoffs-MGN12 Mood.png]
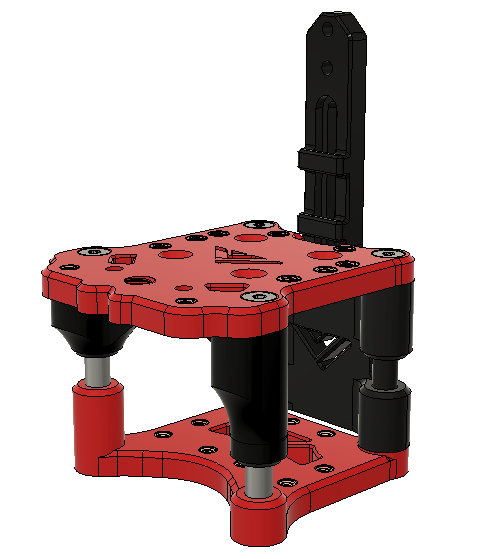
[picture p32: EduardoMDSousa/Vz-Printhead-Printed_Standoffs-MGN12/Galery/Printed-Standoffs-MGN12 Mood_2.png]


Front printed StandOffs

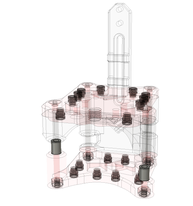
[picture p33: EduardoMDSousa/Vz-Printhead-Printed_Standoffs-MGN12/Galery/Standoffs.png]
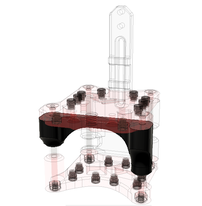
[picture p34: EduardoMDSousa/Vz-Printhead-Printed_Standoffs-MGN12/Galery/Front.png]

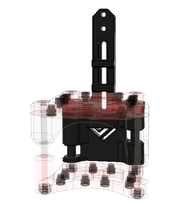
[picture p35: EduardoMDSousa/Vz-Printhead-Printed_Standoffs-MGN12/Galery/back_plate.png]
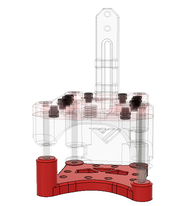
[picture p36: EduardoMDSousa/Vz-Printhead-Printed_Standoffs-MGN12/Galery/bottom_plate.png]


Print orientation redy to slice stl with all parts

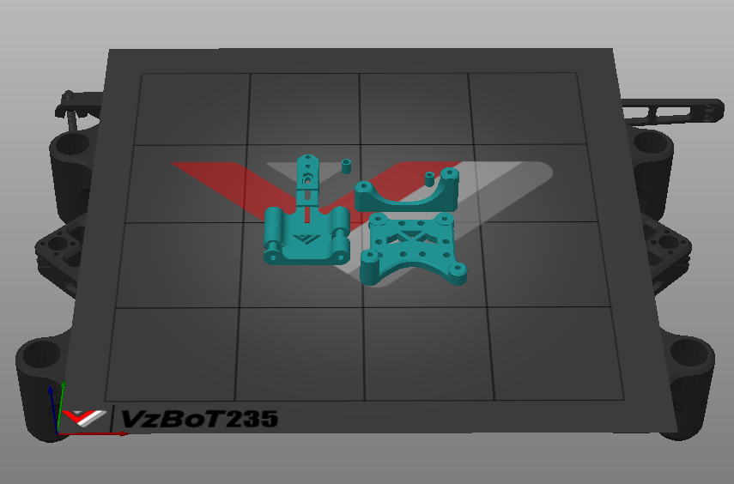
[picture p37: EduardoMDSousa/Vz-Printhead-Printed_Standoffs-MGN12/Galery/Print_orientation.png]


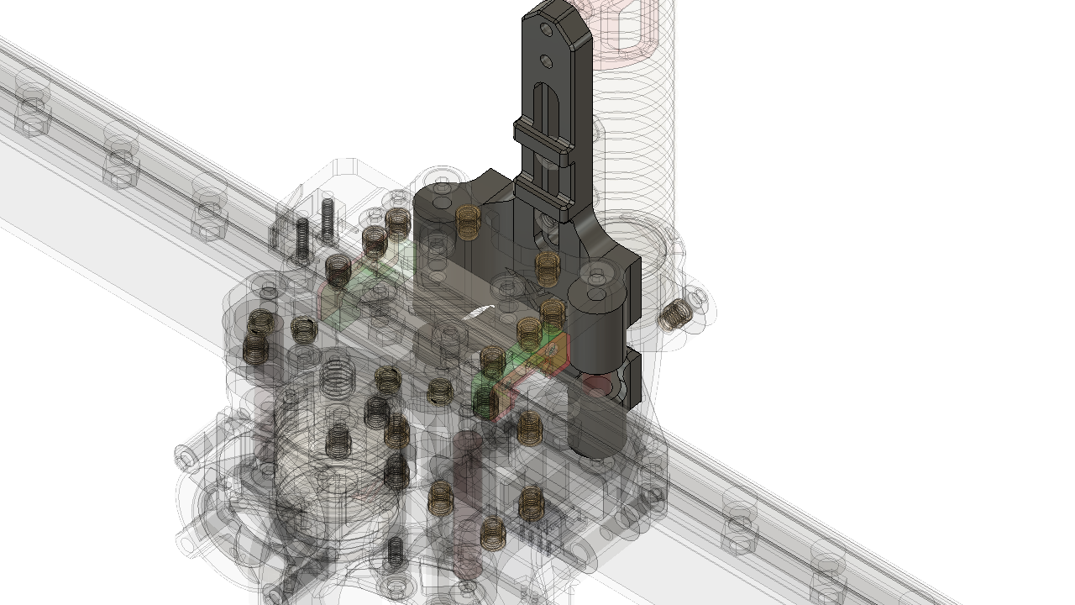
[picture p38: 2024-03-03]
EduardoMDSousa/Vz-Printhead-Printed-MGN12H-Orbiter-1.5-Mood/images/VzBot Printed Print Head MGN12H_MGN9H Hybrid V2 v1.png

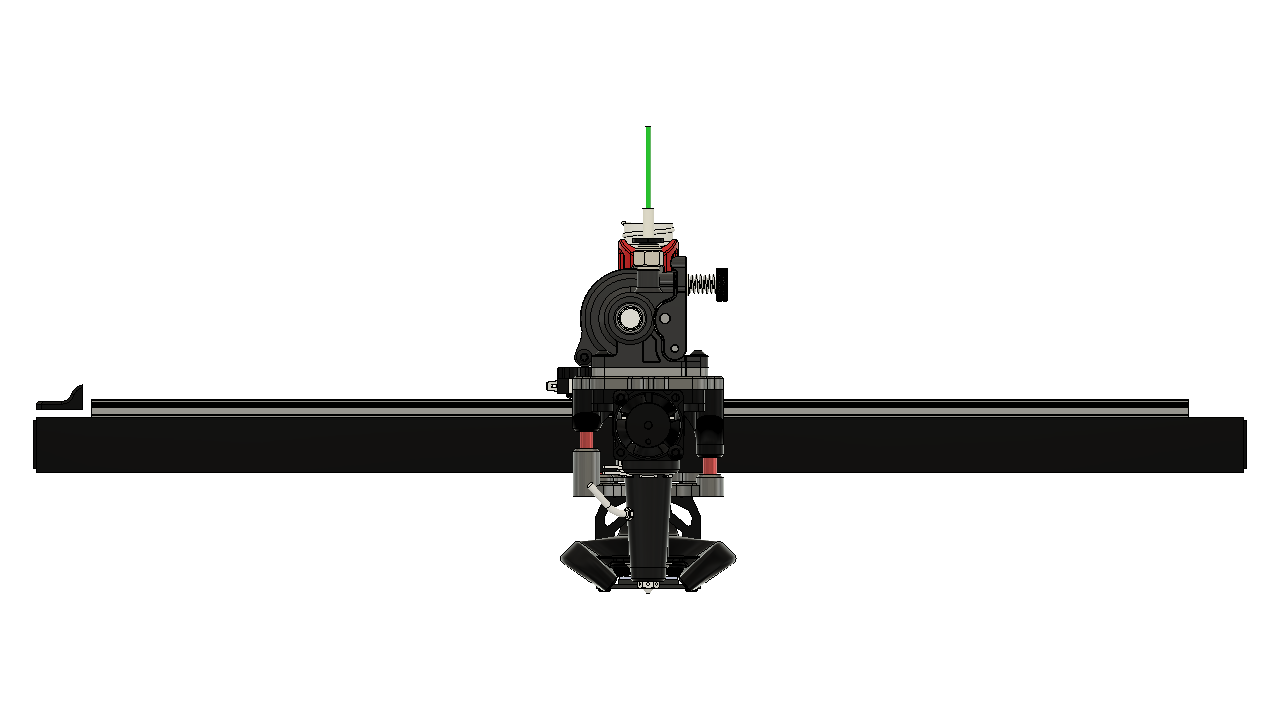
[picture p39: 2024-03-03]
EduardoMDSousa/Vz-Printhead-Printed-MGN12H-Orbiter-1.5-Mood/images/VzBot Printed Print Head MGN12H_MGN9H Hybrid V2 v1 6.png

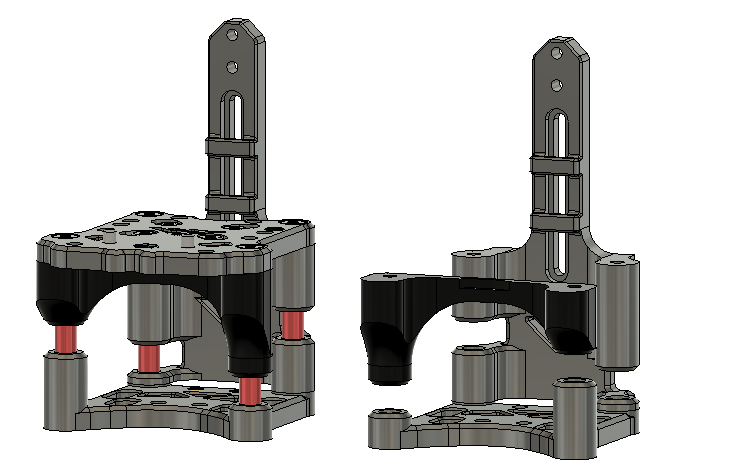
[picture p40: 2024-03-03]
EduardoMDSousa/Vz-Printhead-Printed-MGN12H-Orbiter-1.5-Mood/images/VzBot Printed Print Head MGN12H_MGN9H Hybrid V2 v4 BVL.png

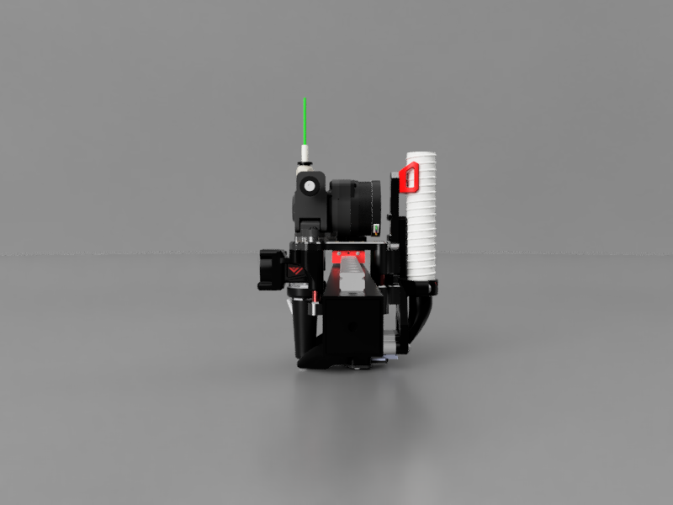
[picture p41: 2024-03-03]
EduardoMDSousa/Vz-Printhead-Printed-MGN12H-Orbiter-1.5-Mood/images/VzBot_Printed_Print_Head_MGN12H_MGN9H_Hybrid_V2_3.png

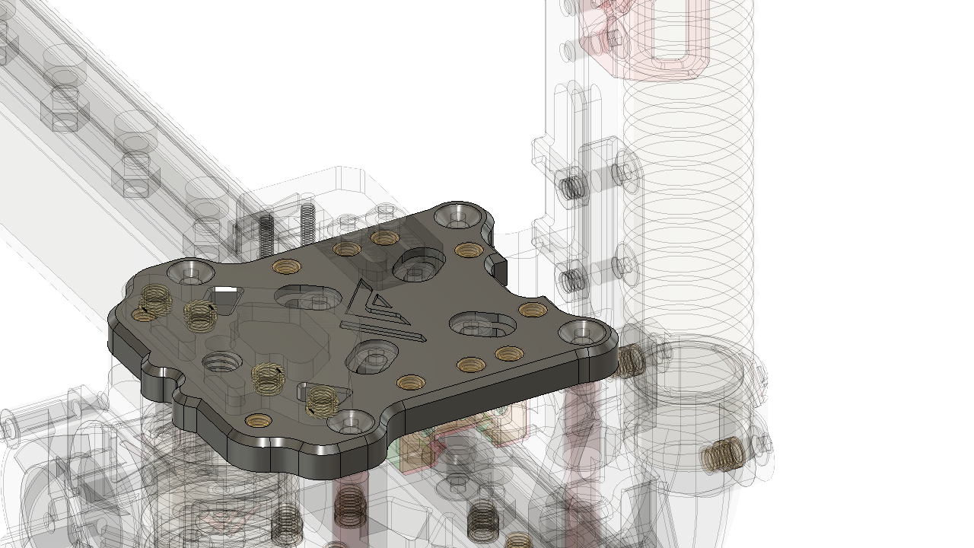
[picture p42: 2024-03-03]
EduardoMDSousa/Vz-Printhead-Printed-MGN12H-Orbiter-1.5-Mood/images/VzBot Printed Print Head MGN12H_MGN9H Hybrid V2 v1 2.png

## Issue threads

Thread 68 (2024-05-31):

Alignment tools do not work on an original X5SA

d4mer, 2024-05-31:
Opening this issue so that others do not print these unnecessarily. They are far too short to work on an X5SA so if you are upgrading your X5SA to VzBot, do not print these

Closed 2025-01-02.

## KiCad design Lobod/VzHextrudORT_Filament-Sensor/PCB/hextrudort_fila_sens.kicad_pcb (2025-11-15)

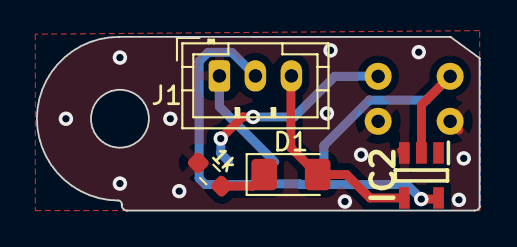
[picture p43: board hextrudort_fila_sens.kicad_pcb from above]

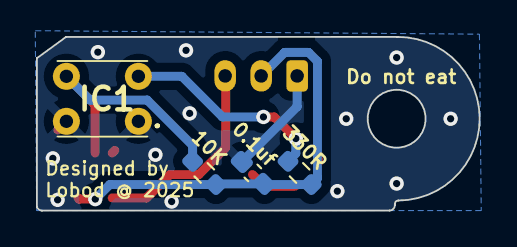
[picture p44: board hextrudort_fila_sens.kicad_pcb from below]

Board: 2 copper layers, 24.6 x 9.6 mm, 8 parts (4 on the bottom side), 6 nets.

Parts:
C2: 0.1uf; C_0603_1608Metric_Pad1.08x0.95mm_HandSolder
D1: LED; LED_1206_3216Metric_Pad1.42x1.75mm_HandSolder
IC1: EE-SX1103; EESX1103
IC2: SN74LVC1G14DBVR; SOT95P280X145-5N
J1: Conn_01x03; JST_PH_B3B-PH-K_1x03_P2.00mm_Vertical
R1: 10K; R_0603_1608Metric_Pad0.98x0.95mm_HandSolder
R2: 1k; R_0603_1608Metric_Pad0.98x0.95mm_HandSolder
R3: 330R; R_0603_1608Metric_Pad0.98x0.95mm_HandSolder

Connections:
+5V: C2.1, IC2.5 (VCC), J1.2, R1.2, R3.1
/SIG: D1.2 (A), IC2.4 (Y), J1.3
GND: C2.2, IC1.1 (K), IC1.4 (E), IC2.3 (GND), J1.1, R2.2
unnamed: D1.1 (K), R2.1
unnamed: IC1.2 (A), R3.2
unnamed: IC1.3 (C), IC2.2 (A), R1.1

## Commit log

2022-01-06 Added Trihorn Mod
    By knarfie
    [trihorn fdm.3MF, trihorn resin.3MF]
2022-01-06 Idler mounts mod
    Idler mounts with shoulder bolt support
    [idler mount left bottom.3MF, idler mount left top.3MF, idler mount right bottom.3MF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]
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2022-02-04 Adding VzBot Skirt (#9)
    [VzBot_Skirt_Left_Front_Skirt_v1.stl, VzBot_Skirt_Left_Rear_Skirt_W-250v-Cat6-Fans_v1.stl, VzBot_Skirt_Left_Rear_Skirt_W-250v-Fans_v1.stl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]
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2022-02-05 Patch to update all Tronxy profiles from their out-of-date 2020 versions. (#10)
    [VzBot.stl]
2022-02-07 Updated Read Me And Stls (#13)
    [VzBot_Skirt_Feet_scalable_spacer_v1.stl, VzBot_Skirt_Left_Rear_Skirt_W-250v-Cat6-Fans_v1.stl, VzBot_Skirt_Left_Rear_Skirt_W-250v-Cat6-Fans_v2.stl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]
2022-02-24 Vzbot Klicky probe (#14)
    [Eva probe mount.step, Eva probe_mount.stl, Klicky Probe + Dock.step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]
2022-02-25 Added Rac's MGN9 gantry
    [Gantry_MGN9_Lower.stl, Gantry_MGN9_Upper.stl]
2022-02-25 Added karnadi's NF Crazy front face 2510 fan with BLTouch mount
    [Front_face_mosquito_2510_fan_bltouch.3mf, bltouch_mount.3mf, universal_face3.stl]
2022-02-25 Added karnadi's VzHextrudort pneumatic coupler
    [vzhextrudort_body_pneumatic.3mf]
2022-02-25 Added SPINAE's Rapido HF mount
    [rapido_mount_30mm_fan.3mf]
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2022-04-16 Adding VZTrident Mod (#17)
    [BTT_MOT_EXP_bracket.stl, DIN_center_support_x2.stl, DIN_frame_mount_x4.stl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]
2022-04-23 Quickdraw has it's own repository. (#20)
    [400_bed_hole_locations.dxf, FL_Bed_Mount.stl, FL_Magnet_Z_10mm_MGN12C.stl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]
2022-04-28 VZ_HextrudORT_High_Motor_Mount_for_EVA (#18)
    * Create README.md
    * Add files via upload
    * Update README.md
    [Top-MGN9-VZ_HextrudORT_MellowAB.stl, V6 Brace Spacer.stl, V6 face clamp Hexudort.stl]
2022-04-28 WaveShare 5inch DSI LCD (#21)
    * initial commit WaveShare 5inch DSI LCD
    * add image
    * update README.md
    [Front Screen Cover.stl, screen mount back.stl]
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2022-05-17 VZ Sexbolt Z endstop (#22)
    [SidePiece.stl]
2022-05-17 adding Yendstop.stl (#29)
    * Create mods
    * Delete mods
    * Create description
    * Rename description to ReadMe
    * Update ReadMe
    * Update ReadMe
    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
    [YendStop.stl]
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2022-05-18 Moved the yendstop to its own folder
    [YendStop.stl]
2022-05-27 Adding Pully gauge and motor support shelf (#31)
    [Motor_pully_gauge_17.25mm.stl, Motor_pully_gauge_8mm.stl, VZ_235_Left_XY_motor_support.stl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]
2022-07-02 Add files via upload
    Changed hole position for the cf tube, was 0.5mm off
    [Gantry_MGN9_Lower.stl, Gantry_MGN9_Upper.stl]
2022-07-02 Endstop for MGN9 on Y
    [Y Endstop MGN9.stl]
2022-07-06 Add tophat for vz235 (#36)
    [Corner_BackLeft.stl, Corner_BackRight.stl, Corner_FrontLeft.stl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]
2022-07-06 Hading 180 door hinges MOD (Take 2) (#35)
    [LeftMotorIdler(RODAM).stl, PulleyMountLeftBottom(RODAM).stl, PulleyMountLeftTop(RODAM).stl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]
2022-09-16 VZ330 Skirts with V0 display (#39)
    [Display_face_insert_v2_x1.stl, Display_shroud_x1.stl, Fan_Duct_v2_x2.stl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]
2022-09-16 Added brace for Dancer so 5015 can't move (#33)
    [Clamp_Heatset.stl, Clamp_Hexnut.stl, Clamp_Hexnut_Frictionfit.stl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]
2022-09-16 Add hot swappable exhaust adapter (#38)
    * Add mdwasp/hot swappable exhaust tube
    * Enlarge cutout for cable channel
    [cap.stl, tube_end.stl, vzbot_235_mount.stl]
2022-09-16 New parts And pic (#37)
    * Hading 180 door hinges MOD (Take 2)
    I had so many fail on my firs sync. I just deleted my first fork and this is the second try at making contribution !!!!
    * Relocated the readme file in the folder
    OUPS! the readme file was on the first level. now it's in the folder of the mod itself!
    * Change orientation of STL Files
    Change orientation to conform to print orientation.
    * Had step files for Hinges
    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
    [V-BeeBotDoorHinge v1.step, V-BeeBotFrameHingeB v1.step, V-BeeBotLeftFrameHinge v1.step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]
2022-09-16 Adding the Beefy X-Endstop mod (#32)
    [X end stopper_beefy.stl, X end stopper_longer.stl]
2022-09-17 Update for Quickdraw and VZK235 and VZK330 (#41)
    [#Right_front_50mm.dxf, 1.4mm M5 spacer.stl, 11mm M5 spacer.stl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]
2022-10-03 Sherpa NF Crazy by Mellow with bracket (#42)
    [face.stl, front_bracket.stl, rear_bracket.stl]
2022-10-03 Renamed to match table
    [face.stl, front_bracket.stl, rear_bracket.stl]
2022-10-24 CPAP back panel tube mount VZ330 (#43)
    [CPAP_back_panel_tube_mount_VZ330.step, CPAP_back_panel_tube_mount_VZ330_part2.stl, CPAP_back_panel_tube_mount_VZ330_part3.stl]
2022-12-20 New Quickdraw version.
    New QD2 due to bed mesh issue's with old.
    [Mount VZBot Low.stl, Mount_section_A_x1_Rev1 Edited.stl, QD2_Dock_Mount.stl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]
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2023-01-09 Add CAD, STLs, and Images
    [AluZ_Wago_Clamp_x2.stl, AluZ_Wago_Mount.stl, VZ330-AluZ-BedWago.f3d]
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2023-01-09 Fix rename error
    [AluZ_Wago_Clamp_x2.stl, AluZ_Wago_Mount.stl, VZ330-AluZ-BedWago.f3d]
2023-01-26 CPAP one piece resin fan ducts
    [CPAP_Trihorn_Fan_Duct_one_piece.step, CPAP_Trihorn_Fan_Duct_w_brace_one_piece.step]
2023-02-07 Delete trihorn spacer For Rapido MGN12H.3mf
    eliminar
    trihorn spacer For Rapido MGN12H.3mf
    error in dimensions
    [trihorn spacer For Rapido MGN12H.3mf]
2023-02-07 Delete trihorn spacer For Rapido MGN12H.stl
    trihorn spacer For Rapido MGN12H.stl
    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
    [trihorn spacer For Rapido MGN12H.stl]
2023-02-07 Add files via upload
    add , trihorn spacer For Rapido MGN12H V2.stl , with corrected stanoff measurements
    [trihorn spacer For Rapido MGN12H V2.stl]
2023-02-07 Add files via upload
    add step V2 with, trihorn spacer For Rapido MGN12H V2 , with corrected stanoff measurement
    [Cariage mgn12 Extra parts V2.step]
2023-02-07 Delete Cariage mgn12 Extra parts.step
    delete outdated step
    [Cariage mgn12 Extra parts.step]
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2023-02-11 Update folder and image for klicky duct
    update
    add Klicky_Trihorn Fan Duct v2 readme
    add klicky image galery for readme
    [carriage mgn12 v2 Beta 8 v1.0.step]
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2023-02-26 Add files via upload
    Vew vertion
    change on magnet hight
    [Klicky_Trihorn Fan Duct v3.3mf]
2023-02-28 New Mount for Vz235.
    [235_Mount_Slide.stl]
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2023-04-26 Adding batch mood Vz-Printhead-Printed_Standoffs-MGN12 (#48)
    * Vz-Printhead-Printed_Standoffs-MGN12_mood
    Add plastic standoffs vertion of the MGN12 Mood
    * add print head pic
    2 pics missing
    Readmi for Vz-Printhead-Printed Printed-Standoffs-MGN12 Mood
    Missin M3 self lock nut pic
    missing m3 x 45 bolt image
    edit Bom hardware readme
    edit readmi add pics and rework
    Add Vz-Printhead-Printed_Standoffs-MGN12 Mood
    edit readmi to correct erros on cli
    add redy all parts bed plate stl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
    [All Parts MGN12 (plastc standoffs).stl, Front v4.1 mgn12 (Plastic Standoffs) (Tubes) (1).stl, Standoffs (Front).stl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]
2023-04-26 X5SA Z Axis component Reuse (#51)
    [X5SA Z.step, X5SA Z.stl, Z Rod Spacer Guide.stl]
2023-04-27 added vzhextrudort heavy backplate (#52)
    my vzhextrudort is using BMG clone gears. spacing will be different with the original BMG gears
    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
    [YendStop.stl, vzhextrudort heavy back plate.stl]
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2023-10-05 Added M4 spool holder mod
    [M4_Spool_Holder.ipt, M4_Spool_Holder.stp, Spool_Holder_M4_Front_Hole.stl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]
2024-02-19 files cleaned up. (#58)
    [1.4mm M5 spacer.stl, 11mm M5 spacer.stl, 8mm_probe_adapter option1.stl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]
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2024-03-03 Create Vz-Printhead-Printed-MGN12H-Orbiter-1.5-Mood (#61)
    add redy all parts bed plate stl
    *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
    [Belt_clip.stl, Cariage mgn12 Extra parts V2.step, Front MGN12H v2.3mf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]
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

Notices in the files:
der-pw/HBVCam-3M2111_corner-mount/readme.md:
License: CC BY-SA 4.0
